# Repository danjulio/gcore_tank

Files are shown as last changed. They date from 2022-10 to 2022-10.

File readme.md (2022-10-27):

# gCore controlled ESP32-CAM tank

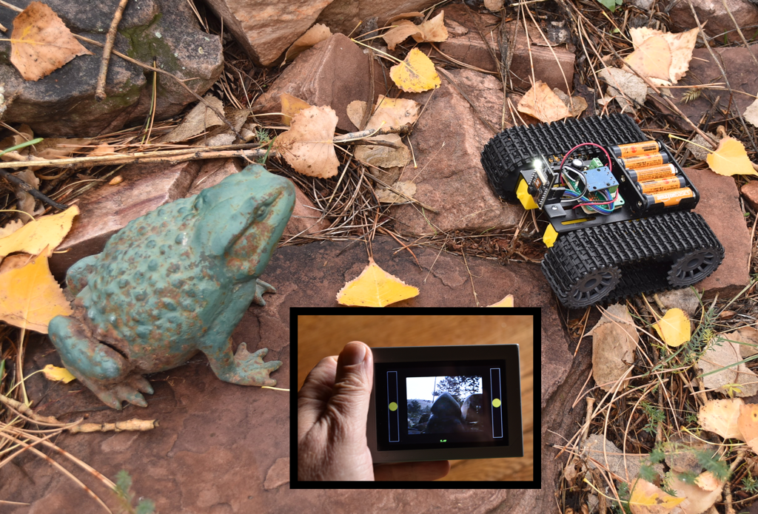
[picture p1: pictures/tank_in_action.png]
Tank in action


A simple remote controlled tank (or car) based on the ubiquitous ESP32-CAM module using [gCore](https://github.com/danjulio/gCore) as a hand-held controller with live video feed.

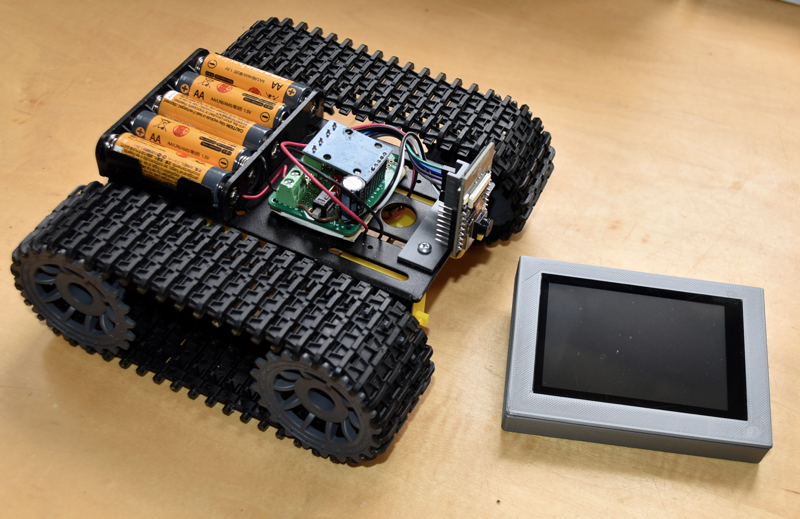
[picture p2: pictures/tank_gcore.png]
Close up of tank


The vehicle consists of the following parts.  I used inexpensive components found on Amazon but any number of bodies, motors and drivers can be substituted.

1. AI-Thinker ESP32-CAM - OV2640 sensor, ESP32, PSRAM
2. Vehicle Body - Driven with two DC brushed motors, one on each side.  Can be a tank or car style.  My [tank](https://www.amazon.com/dp/B09TFSKQ7J) claims to have 3-6V motors (but they really need 6+ volts to move the tank).
3. Dual H-Bridge Driver - Matched to the power supply and motors and capable of being driven by 3.3V logic.  My HiLetgo [board](https://www.amazon.com/dp/B00M0F243E) uses a L9110S H-bridge chip.  See note below about removing some pull-up resistors if you use this board.
4. Battery Pack - Capable of powering the vehicle but within the range of the ESP32-CAM 5V input (feeding an AMS1117 regulator with a probable max of 12V).  I used a 5 AA pack.
5. Misc components - Power switch, Bulk Capacitor (I used 1000 uF), a pair of 0.1 uF/50V caps for the motors, proto board, hook-up wire and dupont cables, misc mounting hardware.
6. gCore (from [Group Gets](https://www.groupgets.com))
7. [Optional] 3D printed mount for ESP32-CAM

Code for the ESP32-CAM and gCore are ESP32 Arduino sketches.  I used Arduino 1.8.19 with the ESP32 1.0.6 package along with several libraries that may be found in the gCore repository or other of my repositories.

The ESP32-CAM advertises a WiFi SSID that the gCore connects to.  The system uses a socket to transfer a mjpeg video stream and control information.  The dual-touch capability of the gCore touchscreen is used to provide two sliders, one for each motor, with spring-back on release.  The gCore power button short-press is used to turn on and off the ESP32-CAM flash LED acting as a headlight.

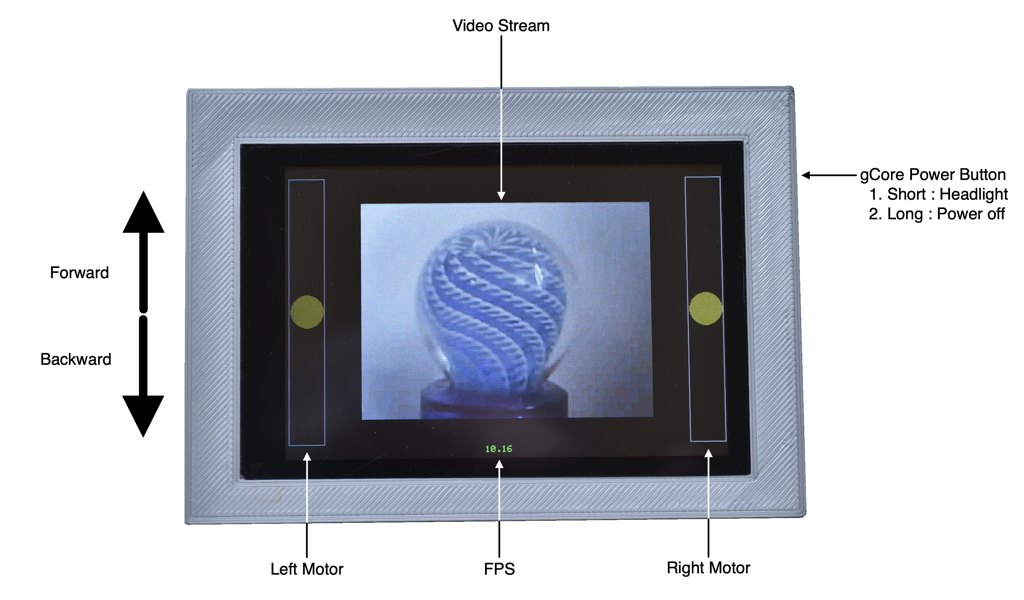
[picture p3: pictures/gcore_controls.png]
Control Description


This repository contains the Arduino sketches and an OpenSCAD design for the ESP32-CAM mount.

## Programming Notes

1. Configure the Arduino environment for an ESP32 WROVER module and set the serial monitor to 115200 baud.
2. Follow the many online guides for loading the ```esp32_cam_tank``` sketch into the ESP32-CAM.  This requires using an external 3.3V USB-UART board or cable connected to the ESP32-CAM TX/RX/5V/GND lines.  Ground IO0 when applying power to enter bootloader mode.  Program the ESP32-CAM before connecting to the tank electronics.
3. Turn on gCore before loading the ```gcore_tank_controller``` sketch.  Select the serial port associated with gCore when it is powered.

## Wiring Diagram

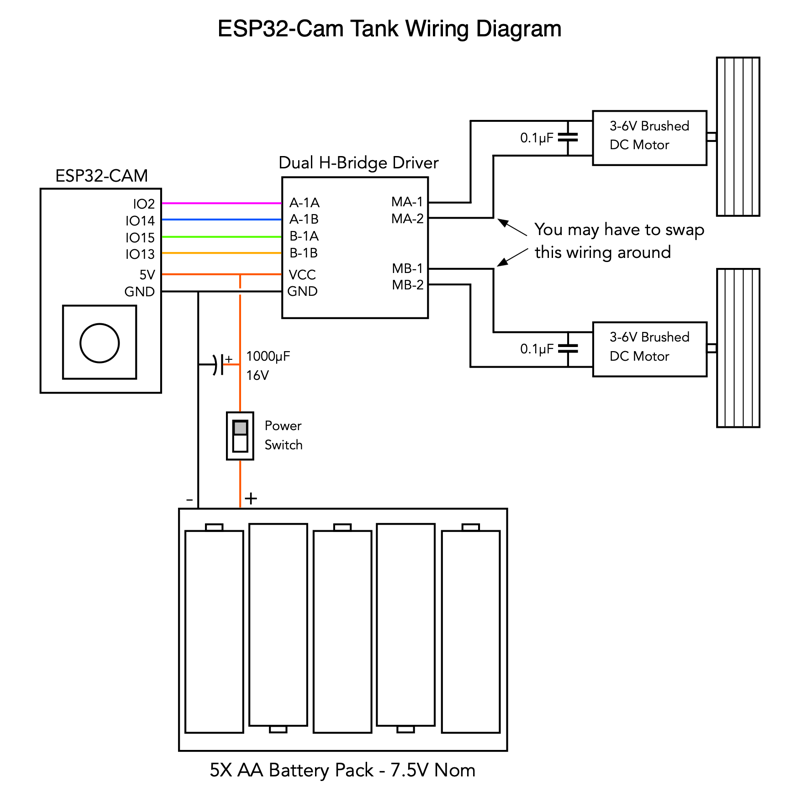
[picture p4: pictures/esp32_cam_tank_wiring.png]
Wiring Diagram

Spare GPIO signals on the ESP32-CAM are used to generate 25 kHz PWM signals to control the speed of each motor (a pair for each motor).  You may have to swap either the motors or their wiring connections to the Dual H-Bridge driver after you assemble the vehicle.  It will be obvious when you first try to drive it :-)

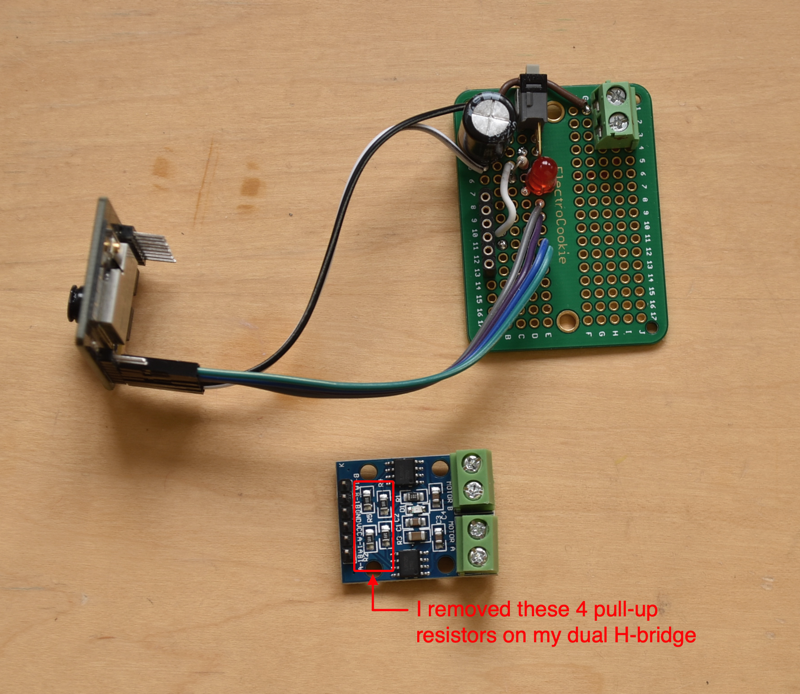
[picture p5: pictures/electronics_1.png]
Wired Boards

The Dual H-Bridge Driver includes four 10-kohm resistors on the inputs connected to VCC.  Since VCC is connected to the 7.5V battery pack these pull-ups will strain the ESP32 GPIO pads.  I removed the four resistors.  A side-effect is that the motors might run for a second before the code starts running on the ESP32 and sets all four outputs low initially.

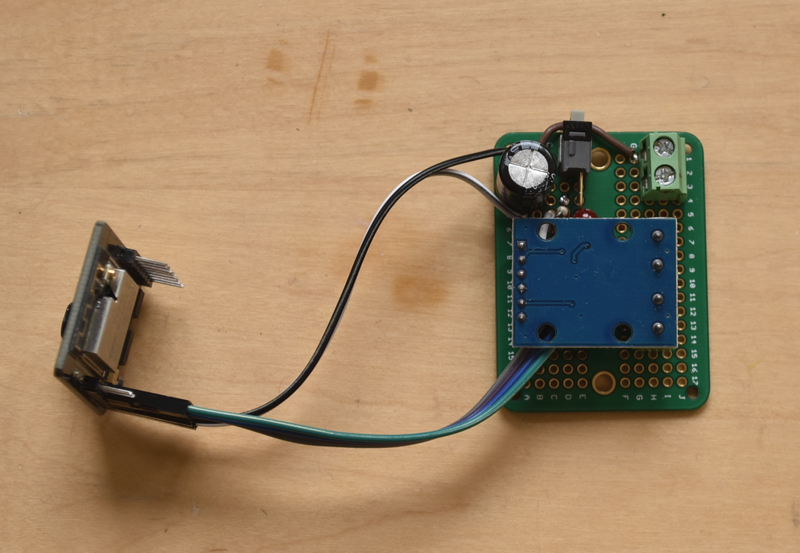
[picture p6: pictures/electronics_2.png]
Assembled Electronics


## ESP32-CAM Mount
I designed and 3D printed a very simple mount to hold the ESP32-CAM perpendicular to the tank mounting plate so the camera (and LED) can face forward.

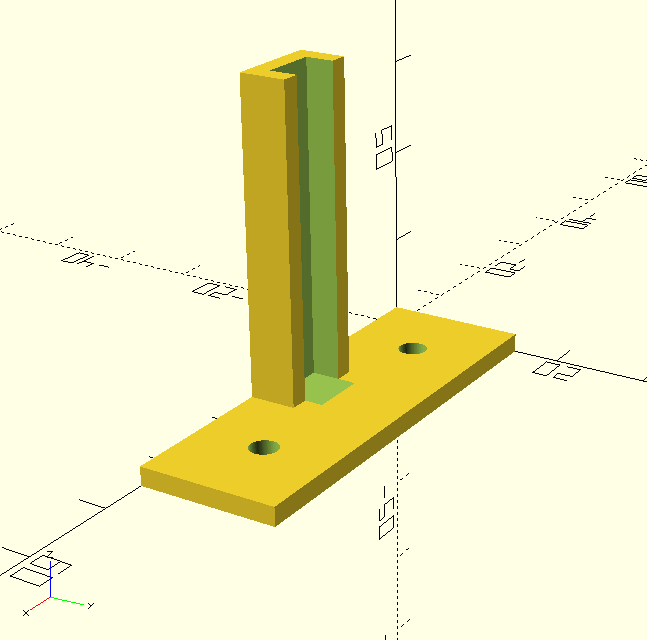
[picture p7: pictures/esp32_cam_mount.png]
3D Printed mount OpenSCAD Design


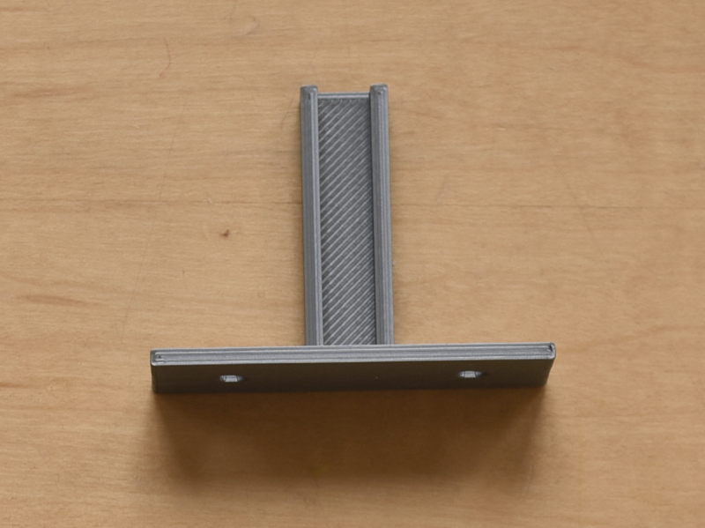
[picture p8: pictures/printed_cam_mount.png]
3D Printed mount


## Assembly Pictures

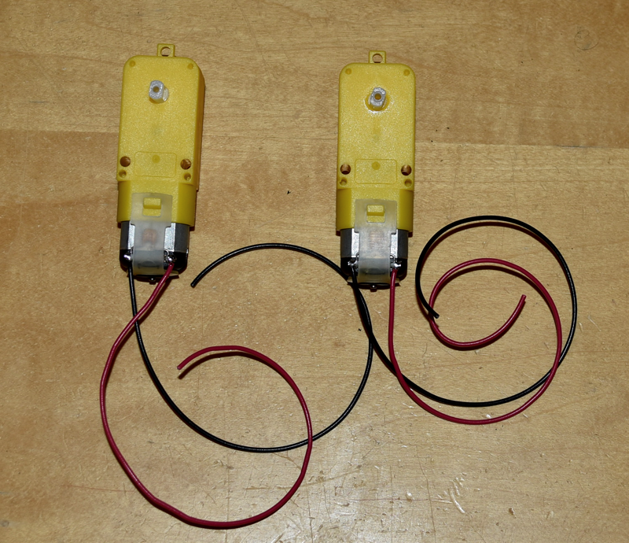
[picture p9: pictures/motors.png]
Motors with capacitors

I added a 0.1 uF (50V) capacitor across the terminals of the motors to reduce electrical noise.  You can see them under the restraining straps.

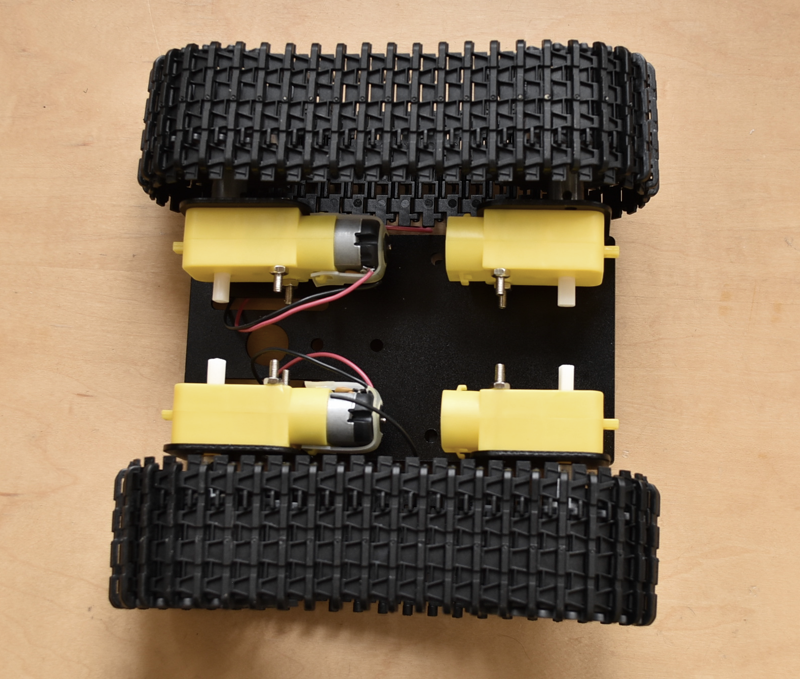
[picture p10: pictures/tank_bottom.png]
Motors mounted

The tank kit had four motors with gear assemblies.  I used all four gear assemblies but removed two motors.

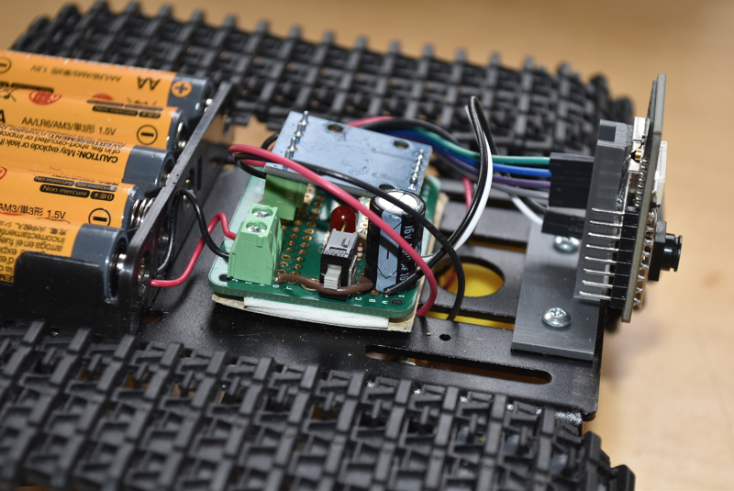
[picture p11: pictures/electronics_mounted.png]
Electronics mounted to vehicle

Both the battery pack and and circuit board were attached to the vehicle body using strong 3M double sticky tape.  I also taped a piece of cardboard under the circuit board to prevent shorts.  The ESP32-CAM Mount is screwed to the vehicle body and the ESP32-CAM is stuck to it using double sticky tape on the ESP32 module.

## Final Comments
My build is far from optimized.  The motors are underpowered for the vehicle and require high PWM values (> 50%) to even start moving.  You can see a map function in the ```motor_set``` function (```motors``` tab in the ```esp32_cam_tank``` sketch) where I map the incoming speed value to smaller range of the PWM period (speed of 32-255 to 10-bit PWM values 640-1023).  Probably a more expensive vehicle base and matching drivers and power supply would work better.

Decoding the mjpg stream is expensive on the gCore's ESP32 and variable depending on how complex the image is.  I generally got less than 12 FPS.  It is clear that many things affect the WiFi connection occasionally slowing the connection further.  This makes using the video feed more difficult to use when driving the vehicle out of sight.  

Despite these short comings this project was a fun build and I hope gives you ideas for your own builds and code to hack away at.

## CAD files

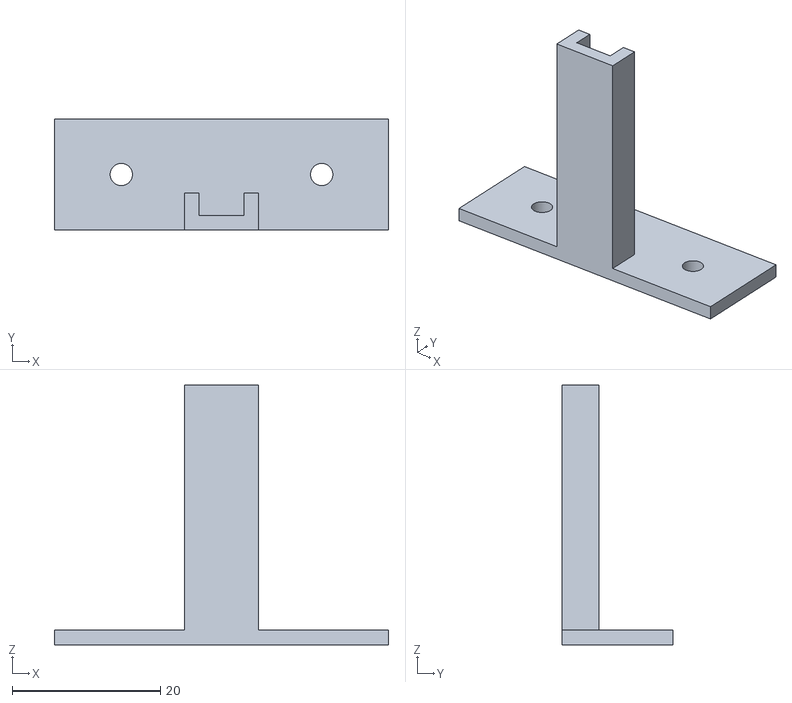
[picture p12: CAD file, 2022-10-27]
esp32_cam_mount/esp_cam_car_mount.stl
45.0 x 15.0 x 35.0

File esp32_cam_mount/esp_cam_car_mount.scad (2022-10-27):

//
// Quick & Dirty ESP-CAM mount for remote controlled car project
//

width = 45;
length = 15;
height = 2;

pillar_width = 10;
pillar_depth = 5;
pillar_height = 35;

screw_distance = 27;
screw_diameter = 3;

difference() {
    // mount parts
    union() {
        // Base
        cube([width, length, height]);
        
        // Pillar
        translate([(width/2) - (pillar_width/2), 0, 0]) {
            cube([pillar_width, pillar_depth, pillar_height]);
        }
    }
    
    // Screw mounting holes
    translate([(width - screw_distance)/2, length/2, -1]) {
        cylinder(h = height + 2, d = screw_diameter, $fn = 120);
    }
    
    translate([width - (width - screw_distance)/2, length/2, -1]) {
        cylinder(h = height + 2, d = screw_diameter, $fn = 120);
    }
    
    // Pillar cut-out (to save print time)
    translate([(width/2) - (pillar_width/2) + 2, 2, height]) {
        cube([pillar_width - 4, pillar_depth, pillar_height]);
    }
}

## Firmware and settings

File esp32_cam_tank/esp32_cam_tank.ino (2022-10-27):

/*
 * Remote control car/tank controller based on an ESP32-CAM from AI-Thinker.  Streams video to a remote control
 * which controls two motors for left/right drive and the ESP32-CAM flash LED as a headlight.
 * 
 *  - Generates a WiFi hotspot named "ESP32-CAM" with password "esp32cam"
 *  - Opens a socket to communicate with an external remote control
 *  - When connected sends a QVGA sized (320x240 pixel) MJPG stream over the socket to the remote control
 *  - Inteprets a simple ASCII command set for motor and LED control
 *    
 * Command set strings are terminated with a <CR> (Carriage Return - hex value 0x0D)
 *    M<N>=<V>  - <N> = 1 or 2 for motor channel, V = motor speed -255 to 255 (full reverse to full forward)
 *    L=<V>     - <V> = 0 or 1 to turn the LED off or on
 *  
 * MJPG stream images are delimited by 0xFFD8 and 0xFFD9 byte sequences.
 *  
 * Socket is at IP 192.168.4.1:6001
 *  
 * Designed to work with brushed DC motors controlled by a typical H-bridge motor driver that takes a
 * direction two 25 kHz PWM pins for control of each motor.  Put a 0.1 uF cap across the terminals of each  
 * motor.  You'll probably have to fool around with the polarity of each motor after you build your tank
 * and load the code to get them going in the correct direction.  See the github repository for more information.
 *  
 * The small red LED on the AI Thinker board is used as status.
 *  
 * Power on this controller first and then connect to it with the remote control.
 * 
 * Can be built using either the AI-Thinker or WROVER board types in Arduino.  The AI-Thinker ESP32-CAM
 * board requires an external USB-UART interface and manually grounding IO0 when powering on to enter bootloader
 * mode.  It is most helpful to disconnect the motor/H-bridge circuitry when building if you don't want the
 * tank crawling off your desk...
 *  
 * Copyright 2022 Dan Julio.  All rights reserved.
 *  
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
 * You should have received a copy of the GNU General Public License
 * along with this program.  If not, see <https://www.gnu.org/licenses/>.
 */
#include "esp_camera.h"
#include <WiFi.h>

// ==========================================================================
// User configuration
//

//
// Pins (configured for AI-Thinker ESP32-CAM)
//

// Camera pins
#define PWDN_GPIO_NUM     32
#define RESET_GPIO_NUM    -1
#define XCLK_GPIO_NUM      0
#define SIOD_GPIO_NUM     26
#define SIOC_GPIO_NUM     27
#define Y9_GPIO_NUM       35
#define Y8_GPIO_NUM       34
#define Y7_GPIO_NUM       39
#define Y6_GPIO_NUM       36
#define Y5_GPIO_NUM       21
#define Y4_GPIO_NUM       19
#define Y3_GPIO_NUM       18
#define Y2_GPIO_NUM        5
#define VSYNC_GPIO_NUM    25
#define HREF_GPIO_NUM     23
#define PCLK_GPIO_NUM     22

// Headlight LED
const int pin_led = 4;

// Motor Control pins
const int pin_m1_pwmA = 2;
const int pin_m1_pwmB = 14;
const int pin_m2_pwmA = 15;
const int pin_m2_pwmB = 13;

// Motor PWM frequency
#define PWM_FREQ  25000

// Status LED
const int pin_status = 33;




// ==========================================================================
// Internal global constants (shouldn't have to be changed)



//
// Camera configuration
//
#define XCLK_FREQ_HZ 16500000;


//
// Network configuration
//
#define PORT 6001

//
// Maximum jpeg image size (images are stored in PSRAM)
// We choose a very large value compared to the typical size of images because we have
// plenty of room up there in PSRAM!
//
#define MAX_JPG_LEN (128 * 1024)

//
// Wifi configuration
//
const char* ssid = "ESP32-CAM";
const char* password = "esp32cam";



// ==========================================================================
// Global variables
//

// State
bool is_connected = false;

// Jpeg image descriptor
typedef struct {
  bool img_ready;
  int img_len;
  uint8_t* img;
} img_descT;

// Jpeg image double buffer - One side is loaded with the next incoming image
// while the other side is being decoded and displayed
img_descT imgs[2];

// Tasks running on different CPUs
TaskHandle_t cam_task_handle;
TaskHandle_t socket_task_handle;

// Socket interface
WiFiServer wifiServer(PORT);



// ==========================================================================
// Arduino entry points
//
void setup() {
  Serial.begin(115200);
  Serial.println("esp32_cam_tank");

  // Allocate the image buffers in PSRAM
  imgs[0].img_ready = false;
  imgs[0].img = (uint8_t*) heap_caps_malloc(MAX_JPG_LEN, MALLOC_CAP_SPIRAM);
  if (imgs[0].img == NULL) {
    Serial.println("Malloc 0 failed");
    error_blink();
  }
  imgs[1].img_ready = false;
  imgs[1].img = (uint8_t*) heap_caps_malloc(MAX_JPG_LEN, MALLOC_CAP_SPIRAM);
  if (imgs[1].img == NULL) {
    Serial.println("Malloc 1 failed");
    error_blink();
  }

  // We assume that these init functions will be successful (no reason they shouldn't be)
  led_init();
  motor_init();
  wifi_init();
  
  // Blink the status LED as a hello
  led_set_status_on();
  delay(1000);
  led_set_status_off();

  // Hang with a fast status blink if we can't initialize the camera
  if (!camera_init()) {
   error_blink();
  }

  // Finally start tasks
  xTaskCreatePinnedToCore(camera_task, "cam_task", 8192, NULL, 1, &cam_task_handle, 1);       // App CPU
  xTaskCreatePinnedToCore(socket_task, "socket_task", 4096, NULL, 1, &socket_task_handle, 0); // Protocol CPU
  Serial.println("esp32_cam_tank ready to go");
}


void loop() {
  // Main loop does nothing
  delay(1000);
}


// ==========================================================================
// Subroutines
//

// Called on a fatal error - does not return
void error_blink()
{
  while (1) {
    led_set_status_on();
    delay(100);
    led_set_status_off();
    delay(100);
   }
}

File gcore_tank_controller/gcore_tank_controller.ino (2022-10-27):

/*
 * Remote controller for ESP32-CAM-based 2-motor car/tank using gCore to 
 * display the mjpg stream and control the motors and LED headlight using
 * the dual-touch capability of the touchscreen controller.  Designed to 
 * work with the "esp32_cam_tank" sketch running on the ESP32-CAM.
 * 
 * The program displays a pair of sliders on either side of a 320-240 pixel
 * video feed from the ESP32-CAM.  Each slider controls one motor allowing for
 * speed control both backwards and forwards (tank-like).  The gCore power button
 * is re-purposed as a headlight on/off toggle.  Hold it down for five seconds
 * to switch gCore off.
 * 
 * Looks to connect to a WiFi network with the SSID "ESP32-CAM" and password
 * "esp32cam". 
 * 
 * Requires the following libraries:
 *    1. Bodmer's TFT_eSPI library ported to gCore (download from
 *       https://github.com/danjulio/TFT_eSPI)
 *    2. gCore library (https://github.com/danjulio/gCore2)
 *    3. TJpg_Decoder library
 *
 * Copyright 2022 Dan Julio.  All rights reserved.
 *  
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
 * You should have received a copy of the GNU General Public License
 * along with this program.  If not, see <https://www.gnu.org/licenses/>.
 */
#include "gCore.h"
#include <TFT_eSPI.h>
#include <TJpg_Decoder.h>
#include <WiFi.h>
#include <Wire.h>


// ==========================================================================
// User configuration
//

//
// Maximum jpeg image size (images are stored in PSRAM)
// We choose a very large value compared to the typical size of images because we have
// plenty of room up there in PSRAM!
//
#define MAX_JPG_LEN (128 * 1024)

//
// Uncomment to use eSPI_TFT DMA
//
#define USE_DMA


//
// Slider touch sense and draw coordinates
//   Touch detection area is wider than displayed slider because fingers are fat and
//   that allows for more success as the user slides their fingers up and down alongside
//   the image.
#define SLIDER_TOUCH_WIDTH   80
#define SLIDER_TOUCH_HEIGHT  256
#define SLIDER_TOUCH_1_TOP   ((320 - SLIDER_TOUCH_HEIGHT) / 2)
#define SLIDER_TOUCH_1_LEFT  0
#define SLIDER_TOUCH_2_TOP   ((320 - SLIDER_TOUCH_HEIGHT) / 2)
#define SLIDER_TOUCH_2_LEFT  (480 - SLIDER_TOUCH_WIDTH)

#define SLIDER_DRAW_WIDTH    40
#define SLIDER_DRAW_RADIUS   ((SLIDER_DRAW_WIDTH - 2)/2 - 1)
#define SLIDER_DRAW_1_TOP    (SLIDER_TOUCH_1_TOP - (SLIDER_DRAW_WIDTH/2))
#define SLIDER_DRAW_1_BOT    (SLIDER_TOUCH_1_TOP + SLIDER_TOUCH_HEIGHT + (SLIDER_DRAW_WIDTH/2))
#define SLIDER_DRAW_1_LEFT   0
#define SLIDER_DRAW_1_RIGHT  (SLIDER_DRAW_1_LEFT + SLIDER_DRAW_WIDTH - 1)
#define SLIDER_DRAW_1_CENTER (SLIDER_DRAW_1_LEFT + (SLIDER_DRAW_WIDTH/2))
#define SLIDER_DRAW_2_TOP    (SLIDER_TOUCH_2_TOP - (SLIDER_DRAW_WIDTH/2))
#define SLIDER_DRAW_2_BOT    (SLIDER_TOUCH_2_TOP + SLIDER_TOUCH_HEIGHT + (SLIDER_DRAW_WIDTH/2))
#define SLIDER_DRAW_2_LEFT   (480 - SLIDER_DRAW_WIDTH)
#define SLIDER_DRAW_2_RIGHT  (SLIDER_DRAW_2_LEFT + SLIDER_DRAW_WIDTH - 1)
#define SLIDER_DRAW_2_CENTER (SLIDER_DRAW_2_LEFT + (SLIDER_DRAW_WIDTH/2))


//
// Wifi SSID/password strings - change these to connect to a different source
//
#define WIFI_SSID "ESP32-CAM"
#define WIFI_PASS "esp32cam"

//
// Stream URL string - change this to connect to a different source.  It should
// point to a raw mjpeg stream with resolution 480x320 or less.
//
#define REMOTE_IP   "192.168.4.1"
#define REMOTE_PORT 6001


// ==========================================================================
// Global variables
//

// Hardware objects
gCore gc;
TFT_eSPI tft = TFT_eSPI();


// Jpeg image descriptor
typedef struct {
  bool img_ready;
  int img_len;
  uint8_t* img;
} img_descT;

// Jpeg image double buffer - One side is loaded with the next incoming image
// while the other side is being decoded and displayed
img_descT imgs[2];

// Headlight button press detected to pass between tasks
bool headlight_button_pressed = false;

// Slider state shared between between tasks
typedef struct {
  int val;
  SemaphoreHandle_t mutex;
} slider_valT;

slider_valT slider_vals[2];


// Tasks running on different CPUs
TaskHandle_t com_task_handle;
TaskHandle_t disp_task_handle;



// ==========================================================================
// Arduino entry points
//
void setup() {
  Serial.begin(115200);

  // Setup gCore (begins Wire)
  gc.begin();
  gc.power_set_brightness(75);
  gc.power_set_button_short_press_msec(50);

  // Configure the LCD driver
  tft.begin();
  tft.setRotation(3);
  tft.fillScreen(TFT_BLACK);
#ifdef USE_DMA
  tft.initDMA();
#endif

  // Say hello
  tft.setTextColor(TFT_GREEN);
  tft.setTextSize(1);
  tft.setCursor(0, 20);
  tft.println("gcore_tank_controller starting");

  // Initialize the touchscreen controller
  if (!ts_begin()) {
    tft.setTextColor(TFT_RED);
    tft.println("Touchscreen initialization failed");
    while (1) {delay(100);}
  }

  // Configure the decoder
  TJpgDec.setJpgScale(1);
  TJpgDec.setSwapBytes(true);  // Fastest way to swap bytes for 16bpp
  TJpgDec.setCallback(draw_pixels);

  // Allocate the image buffers in PSRAM
  imgs[0].img_ready = false;
  imgs[0].img = (uint8_t*) heap_caps_malloc(MAX_JPG_LEN, MALLOC_CAP_SPIRAM);
  if (imgs[0].img == NULL) {
    tft.setTextColor(TFT_RED);
    tft.println("Malloc 0 failed");
    while (1) {delay(100);}
  }
  imgs[1].img_ready = false;
  imgs[1].img = (uint8_t*) heap_caps_malloc(MAX_JPG_LEN, MALLOC_CAP_SPIRAM);
  if (imgs[1].img == NULL) {
    tft.setTextColor(TFT_RED);
    tft.println("Malloc 1 failed");
    while (1) {delay(100);}
  }

  // Setup the slider evaluation logic
  slider_init();

  // Initialize the slider touch values and mutexes
  slider_vals[0].val = 0;
  slider_vals[0].mutex = xSemaphoreCreateMutex();
  slider_vals[1].val = 0;
  slider_vals[1].mutex = xSemaphoreCreateMutex();

  // Connect to the camera
  tft.print("Connecting to ");
  tft.print(WIFI_SSID);
  tft.print(" ... ");
  WiFi.begin(WIFI_SSID, WIFI_PASS);
  while (WiFi.status() != WL_CONNECTED) {
    delay(100);
  }
  tft.println("connected");

  tft.println("Starting tasks");
  delay(1000);   // Delay to let user see

  // Start the display task on the Application CPU.  It will decode and display the
  // JPEG images and slider position.
  // Note: After it starts to draw images code running in the main arduino loop shouldn't
  // draw to the tft
  xTaskCreatePinnedToCore(disp_task, "disp_task", 4096, NULL, 1, &disp_task_handle, 1);
  delay(100);
  
  // Start the communication task on the Protocol CPU.  It will request and process
  // the incoming stream.
  xTaskCreatePinnedToCore(com_task, "com_task", 4096, NULL, 1, &com_task_handle, 0);
}
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

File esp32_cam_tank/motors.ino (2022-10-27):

/*
 * Support functions related to motor control
 */


// ==========================================================================
// Motor constants
//

// PWM channels (avoid using channels also used by the camera library
#define PWM_CH_1A 4
#define PWM_CH_1B 5
#define PWM_CH_2A 6
#define PWM_CH_3B 7

// PWM Bits
#define PWM_NUM_BITS 10



// ==========================================================================
// Motor API
//
void motor_init()
{
  double f;
  
  pinMode(pin_m1_pwmA, OUTPUT);
  if ((f = ledcSetup(PWM_CH_1A, PWM_FREQ, PWM_NUM_BITS)) != PWM_FREQ) {
    Serial.printf("ledcSetup 1A returned %f (expected %d)\n", f, PWM_FREQ);
  }
  ledcAttachPin(pin_m1_pwmA, PWM_CH_1A);
  ledcWrite(PWM_CH_1A, 0);
  
  pinMode(pin_m1_pwmB, OUTPUT);
  if ((f = ledcSetup(PWM_CH_1B, PWM_FREQ, PWM_NUM_BITS)) != PWM_FREQ) {
    Serial.printf("ledcSetup 1B returned %f (expected %d)\n", f, PWM_FREQ);
  }
  ledcAttachPin(pin_m1_pwmB, PWM_CH_1B);
  ledcWrite(PWM_CH_1B, 0);

  pinMode(pin_m2_pwmA, OUTPUT);
  if ((f = ledcSetup(PWM_CH_2A, PWM_FREQ, PWM_NUM_BITS)) != PWM_FREQ) {
    Serial.printf("ledcSetup 2A returned %f (expected %d)\n", f, PWM_FREQ);
  }
  ledcAttachPin(pin_m2_pwmA, PWM_CH_2A);
  ledcWrite(PWM_CH_2A, 0);
  
  pinMode(pin_m2_pwmB, OUTPUT);
  if ((f = ledcSetup(PWM_CH_3B, PWM_FREQ, PWM_NUM_BITS)) != PWM_FREQ) {
    Serial.printf("ledcSetup 2B returned %f (expected %d)\n", f, PWM_FREQ);
  }
  ledcAttachPin(pin_m2_pwmB, PWM_CH_3B);
  ledcWrite(PWM_CH_3B, 0);
}


// motor : select motor (1: m1, 2: m2)
// speed : signed speed value (-255 to 255)
void motor_set(int motor, int speed)
{
  int mapped_speed;

  if (abs(speed) < 32) {
    mapped_speed = 0;
  } else {
    mapped_speed = map(abs(speed), 32, 255, 640, 1023);
  }
  
  if (motor == 1) {
    if (speed < 0) {
      ledcWrite(PWM_CH_1A, 0);
      ledcWrite(PWM_CH_1B, mapped_speed);
    } else {
      ledcWrite(PWM_CH_1A, mapped_speed);
      ledcWrite(PWM_CH_1B, 0);
    }
  } else if (motor == 2) {
    if (speed < 0) {
      ledcWrite(PWM_CH_2A, 0);
      ledcWrite(PWM_CH_3B, mapped_speed);
    } else {
      ledcWrite(PWM_CH_2A, mapped_speed);
      ledcWrite(PWM_CH_3B, 0);
    }
  }
}

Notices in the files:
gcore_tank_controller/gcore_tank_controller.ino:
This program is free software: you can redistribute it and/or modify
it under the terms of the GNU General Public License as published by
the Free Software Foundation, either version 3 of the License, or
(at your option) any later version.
